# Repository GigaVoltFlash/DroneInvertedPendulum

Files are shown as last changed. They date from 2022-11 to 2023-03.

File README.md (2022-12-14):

# Inverted Pendulum on a CrazyFlie Quadcopter
 
Members: Anshuk Chigullapalli, Rishi Patel, Harry Zhao, Bella Watters

### Abstract
The goal of this project is to create a controller capable of balancing an inverted pendulum on the Crazyflie quadcopter. This is implemented by utilizing the provided sensor decks and the Motion Capture (MoCap) system present in the lab environment. A pendulum is mounted atop the drone with a hinge that allows for one angular degree of freedom. The equations of motion for the pendulum-quadcopter system are derived and linearized about the equilibrium point where the pendulum is in an upright position. The pose of the pendulum is estimated using the MoCap system and tracking markers on both the pendulum and drone. This pose data is then incorporated into the system observer. During testing, the angular error of the pendulum is analyzed to quantify error in the controller and observer performance. Time permitting, the system will be made independent of the MoCap system.

### Equations of Motion
See dynamics/dynamics.ipynb for the full derivation. The equations of motion use the existing drone kinematics and dynamics derived for AE 483, with the additional kinematics of the pendulum based on the state of the drone. The assumption is made that the pendulum's movement does not affect the drone's motion.

### PyBullet Simulation
The Pybullet setup used in AE 483 was modified to have hinge object and the pendulum object so that the controller designed can best tested in simulation before being implemented on the MoCap system.

### Using the MoCap System

1) Setup up the drone pendulum system to have three reflectors, one at the tip of the drone, one at the pendulum base, and a third along the x-axis. 
2) Connect to the "MECHKNIGHT" Wifi network with password "f33dback5". 
3) Open a terminal/command prompt and retrieve your IPv4 address on the network. It should look like 192.168.1.XXX.
4) Navigate to the "DroneInvertedPendulum" directory on the desktop of the MoCap PC. Open the "motrack_udp_InvertedPendulum.py" script in NotePad++.
5) Change the address in the "address_list" array variable to the IPv4 you found earlier.
6) Save and close the file
7) Open the Motive Application located on the desktop of the MoCap PC. When prompted, Click Open Existing Project and choose the AE483 calibration file.
8) You should now see the three reflectors on the drone in the window. Please do not change anything in this file.
9) Navigate back to the "DroneInvertedPendulum" directory on the desktop of the MoCap PC. Double click the "motrack_udp_InvertedPendulum.py". You should see a lot of data scrolling through the terminal.
10) Now, head to your personal laptop and navigate to the "DroneInvertedPendulum" folder and open "motrack_udp_receive_data.py" in the editor of your choice. 
11) Run the file in terminal. Angle data should now be printing in the terminal. Try moving the pendulum to see the change in angle.
12) The angle output should read about 0 degrees. If this is not what you see, please follow the troubleshooting guide below.

### MoCap Troubleshooting

If the angle being printed into the terminal is not correct, there are several reasons this could be happening. The number 1 reason is the order of the motion capture balls in the code is not the same as the order being sent from the central MoCap Computer. In order to fix this, rest the drone-pendulum system in the center of the room with the pendulum on the negative side of the drone. Head over to the MoCap Computer and verify the visual is the same as real life. On the drone operator's laptop, open "motrack_udp_receive_data.py" in the editor of choice and uncomment lines 47 and 49. When the script is run, the terminal will output the positions of each reflective ball every 4 seconds. As seen from lines 24-26, the order of positions printed should be reference, tip, and base. It is possible to guess and check until the angle printed out is correct, however using the Motive software is much easier. First, select the reference ball, right click and hover over "Marker Information". You will see the position of the ball. Compare this to the output on the terminal and check if it is the first position vector printed. If not, look to lines 29-31, and swap variable names until the the vector of reference is printed first. Repeat these steps for each ball until the positions are printed out in the correct order. Once done, comment lines 47 and 49 and rerun the script. The angle should now be fixed.

All the changes made to the "motrack_udp_receive_data.py" file must be copied to the "optitrack" function in "flightThreaded.py".

The other most common failure point is too many markers in the motion capture zone. Unfortunately, there is not much that can be done besides asking for all markers to be covered or moved out of the zone. 

### Hardware Changes

The pendulum was made using a 1.6mm diameter aluminum rod with a reflective ball at the top and bottom. This was then connected to the drone with a 3D-printed custom hinge design which allowed the pendulum to swing with one degree of freedom. 

<!-- ### File Structure

* client: Contains scripts used for operating the drone and performing analysis on data collected during flight.
* OptiTrack: Contains scripts used for sending and receiving data between the OptiTrack Computer and drone operator's laptop.
* firmware: Contains the firmware code used to fly the drone. -->

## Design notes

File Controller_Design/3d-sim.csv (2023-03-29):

time | x | y | z | yaw | pitch | roll | r | s
0.0 | 0.0 | 0.0 | 0.3 | 0.0 | 0.0 | 0.0 | 0.03 | 0.02
0.01 | 2.0084410951447158e-07 | 1.3466445430764533e-07 | 0.29999999960883894 | -1.0731963329099353e-06 | 0.001790702987514691 | -0.001202214452896583 | 0.030045515383370244 | 0.020030342820481353
0.02 | 3.171419454388033e-06 | 2.130358130715952e-06 | 0.29999999271410766 | -1.5525829664653888e-05 | 0.006796622993694129 | -0.004578704387928822 | 0.030180005595058304 | 0.020119987647211145
0.03 | 1.55690883168409e-05 | 1.0481792278861291e-05 | 0.29999993060991975 | -6.947840647937329e-05 | 0.014328354375281332 | -0.009703338768981214 | 0.03039771498495607 | 0.020265040850415268
0.04 | 4.74580177424557e-05 | 3.20409574414711e-05 | 0.29999964653388383 | -0.00019303728092004728 | 0.02377925678021328 | -0.01621086797086229 | 0.03069000137831669 | 0.02045959812225133
0.05 | 0.00011149090535126223 | 7.552093506544515e-05 | 0.2999987661335527 | -0.0004132656055661006 | 0.034620201826255775 | -0.023782176228600467 | 0.03104608368682208 | 0.020696193024748285
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

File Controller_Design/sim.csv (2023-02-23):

time | x | z | theta | alpha
0.0 | 0.0 | 3.0 | 0.0 | 0.1
0.01 | 0.0009938099400883637 | 3.0000006623058217 | 0.0049364958703125 | 0.10036815819452741
0.02 | 0.001980513859265013 | 3.000002534223643 | 0.01785329482834154 | 0.1014399566462271
0.03 | 0.0029740529008861856 | 3.00000524960894 | 0.0354881585726039 | 0.1031296137757584
0.04 | 0.0039936200840638625 | 3.000008112113386 | 0.05549341878181503 | 0.10532032309093181
0.05 | 0.005061033014511207 | 3.0000100233548737 | 0.07620478319736403 | 0.10788088842796799
0.06 | 0.006198876411322737 | 3.000009506627721 | 0.09646679100843064 | 0.11067720759489727
0.07 | 0.007429221180049643 | 3.000004806604344 | 0.11550119797720995 | 0.11357995422153294
0.08 | 0.008772772555884037 | 2.9999940300350976 | 0.13280785946838367 | 0.11646947072109015
0.09 | 0.010248333896235398 | 2.999975295748309 | 0.14809018318115996 | 0.11923864090800416
0.1 | 0.011872499139155121 | 2.999946871467003 | 0.16119914236564242 | 0.12179432469073985
0.11 | 0.01365950790932549 | 2.999907284398129 | 0.17209130755373775 | 0.12405779209333848
0.12 | 0.015621213887682136 | 2.9998554001045084 | 0.18079746948825073 | 0.12596448045122238
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

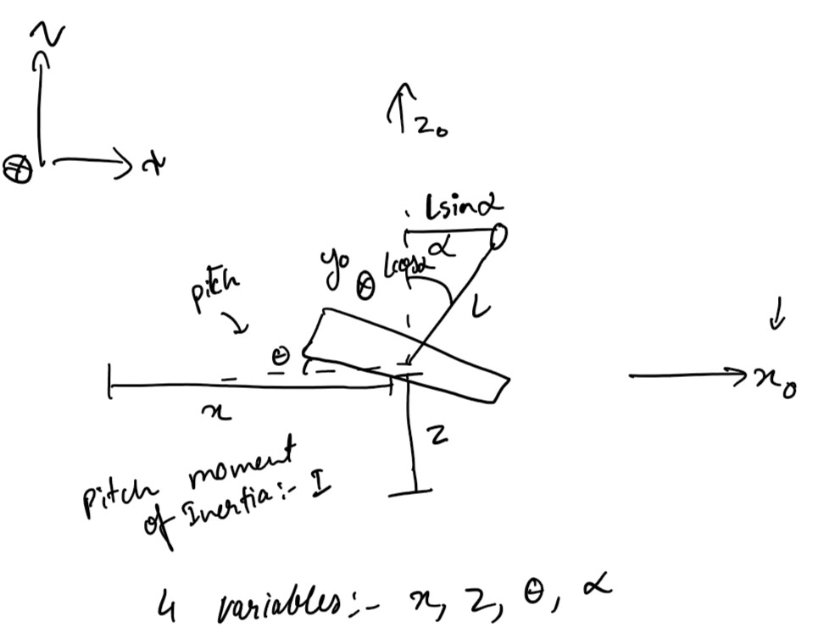
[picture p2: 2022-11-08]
Controller_Design/Inverted_Pendulum_Kinematics.jpg

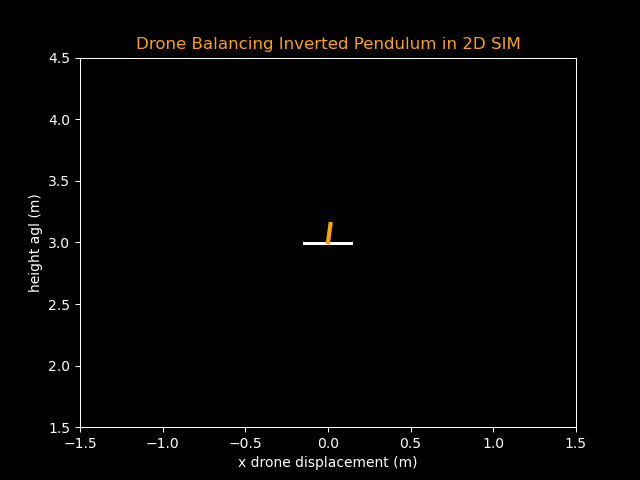
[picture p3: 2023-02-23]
2d_animation.gif

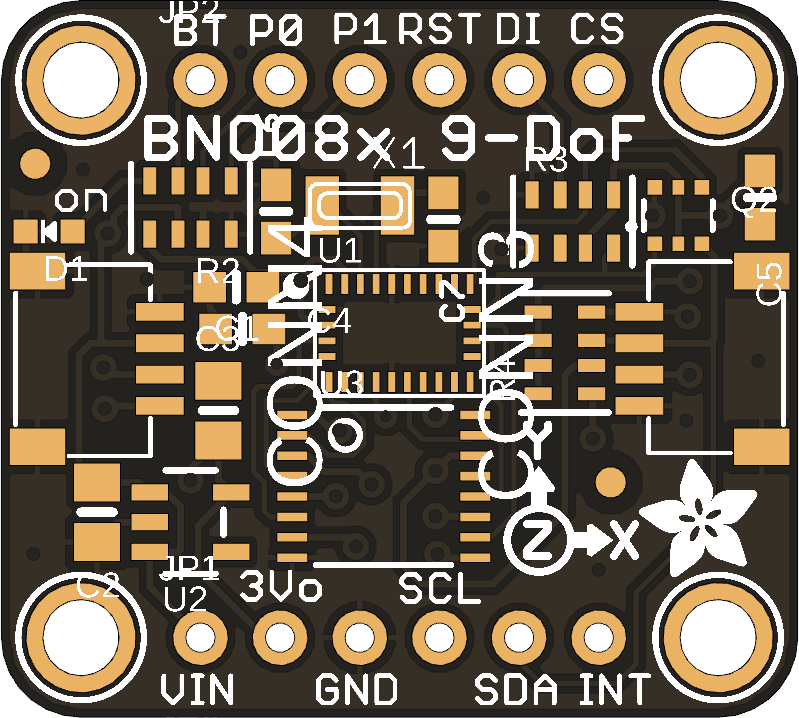
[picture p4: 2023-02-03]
CAD/adafruit-bno085-9-dof-imu-stemma-qt-1.snapshot.3/Adafruit BNO085 STEMMA QT Top.png

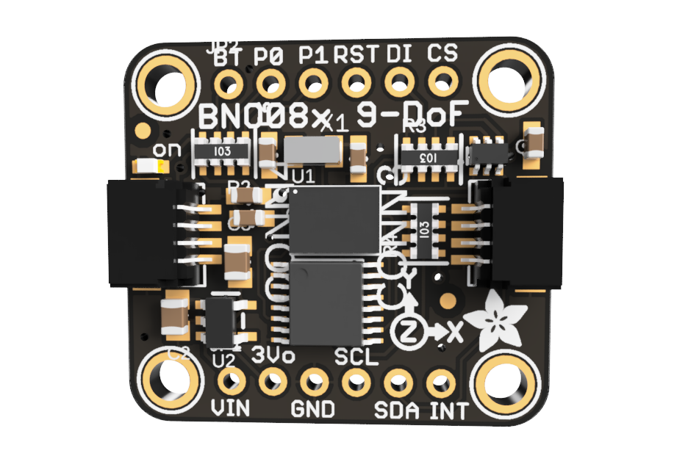
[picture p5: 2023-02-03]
CAD/adafruit-bno085-9-dof-imu-stemma-qt-1.snapshot.3/Adafruit_BNO085_STEMMA_QT.png

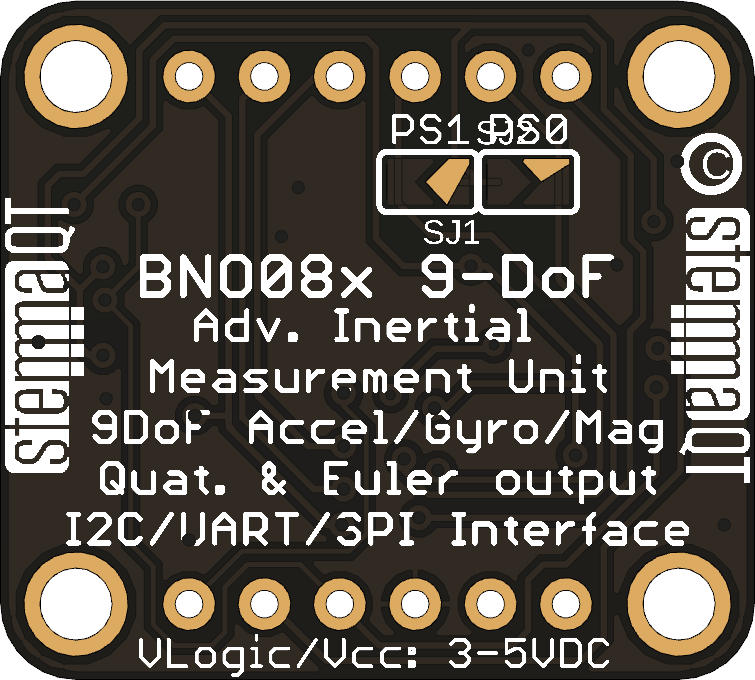
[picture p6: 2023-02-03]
CAD/adafruit-bno085-9-dof-imu-stemma-qt-1.snapshot.3/Adafruit BNO085 STEMMA QT Bottom.png

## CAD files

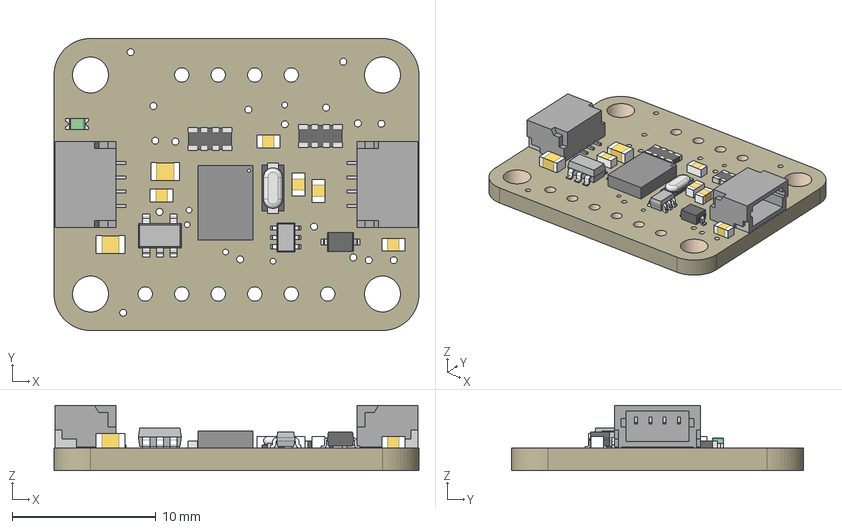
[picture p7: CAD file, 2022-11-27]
CAD/4646 BNO055 Stemma.step
25.4 x 20.3 x 4.53 mm
Board
BNO055
10K x 5
1n4148
10uF x 2
AP2112K-3.3
10K_1 x 2
BSS138
STEMMA_I2C_QT x 2
GREEN

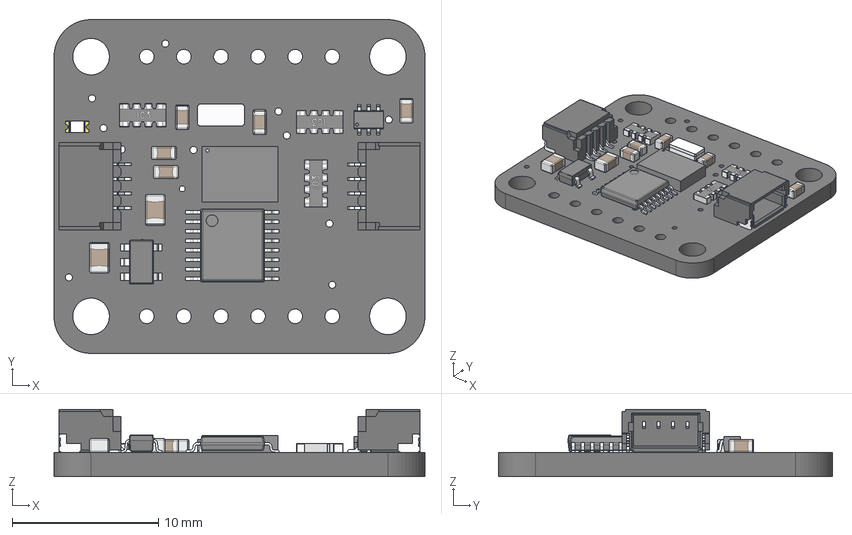
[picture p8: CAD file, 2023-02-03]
CAD/adafruit-bno085-9-dof-imu-stemma-qt-1.snapshot.3/Adafruit BNO085 STEMMA QT.step
25.4 x 22.9 x 4.60 mm
Printed Circuit Board
BNO055-9axis-IMU
BNO085-9axis-IMU
BODY-TSSOP
LEAD-TSSOP x 16
Crystal_XTAL3215_32.768KHz
SOT23-5
BSS138PS
LED 0603 single color
CAPC-0805-T0.95-BN x 2
CAPC-0603-T0.9-BN x 5
YC164_RESPACK x 3
qwicc x 2

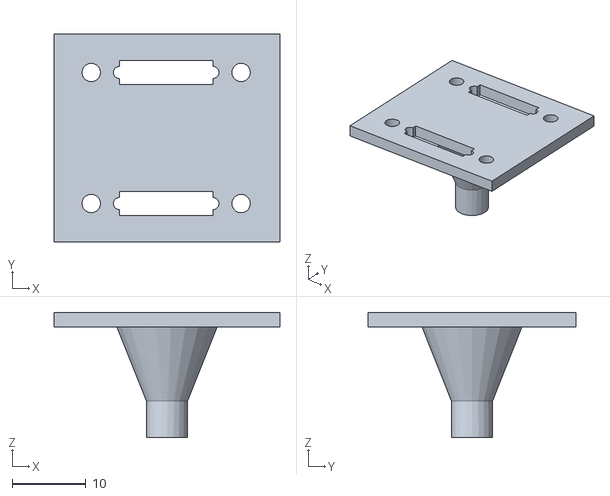
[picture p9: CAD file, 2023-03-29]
CAD/STL Files/BNO_mount_flat.stl
30.6 x 28.2 x 17.0

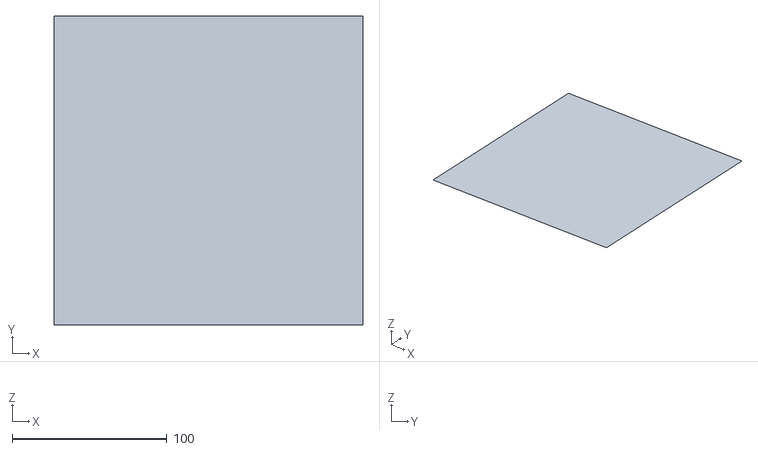
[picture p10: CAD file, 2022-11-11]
Controller_Design/urdf/plane.obj
200.0 x 200.0 x 0

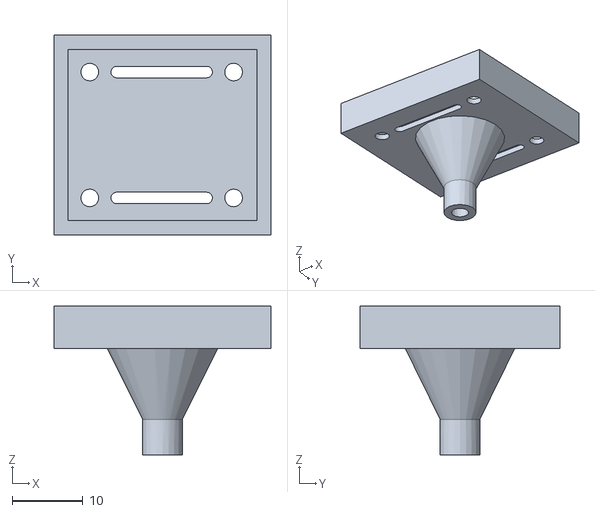
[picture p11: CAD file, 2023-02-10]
CAD/STL Files/BNO_mount_adjusted.stl
30.6 x 28.2 x 21.0

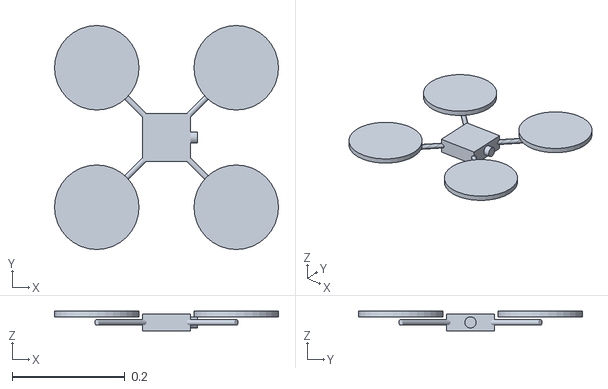
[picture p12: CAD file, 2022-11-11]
Controller_Design/urdf/drone.stl
0.397 x 0.397 x 0.035

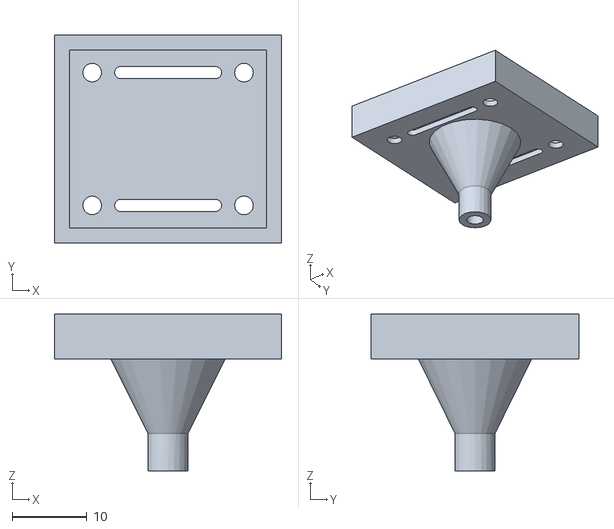
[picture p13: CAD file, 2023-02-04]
CAD/STL Files/BNO_mount.stl
30.4 x 27.9 x 21.0

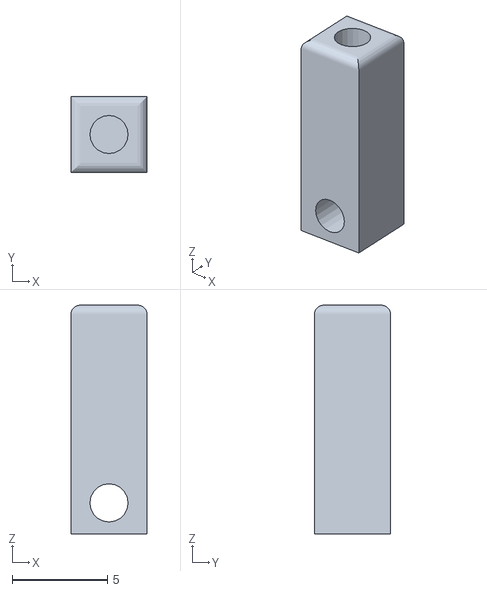
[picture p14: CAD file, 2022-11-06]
CAD/STL Files/SwivelBlock.stl
4.00 x 4.00 x 12.0

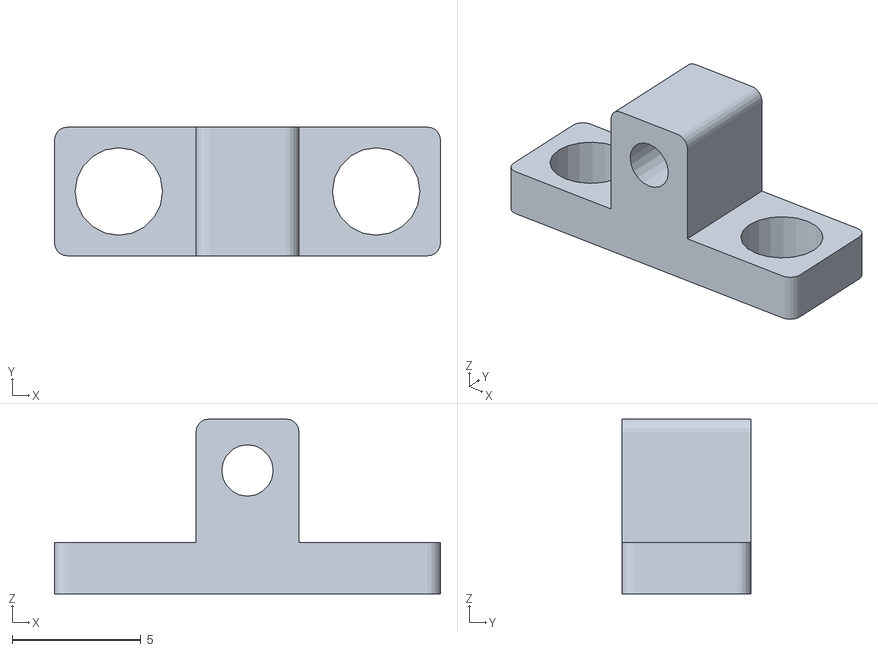
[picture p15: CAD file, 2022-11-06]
CAD/STL Files/SwivelBase.stl
15.0 x 5.00 x 6.80

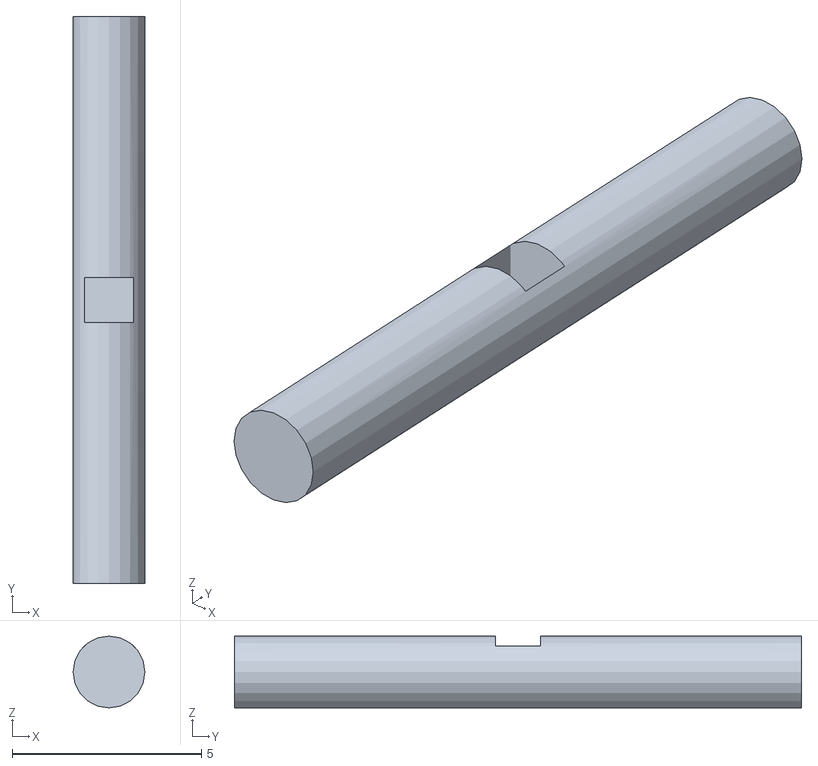
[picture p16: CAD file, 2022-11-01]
CAD/STL Files/SwivelPeg.stl
1.90 x 15.0 x 1.90

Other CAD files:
CAD/10K.prt
CAD/10K_1.prt
CAD/10uF.prt
CAD/1n4148.prt
CAD/32.768.prt
CAD/4646 BNO055 Stemma_step.prt
CAD/AP2112K-3.3.prt
CAD/BNO055.prt
CAD/BNO_mount.prt
CAD/BNO_mount_assembly.prt
CAD/BSS138.prt
CAD/Board.prt
CAD/GREEN.prt
CAD/PRT Files/CrazyflieLayout.prt
CAD/PRT Files/MoCapDeck.prt
CAD/PRT Files/PendulumAssembly.prt
CAD/PRT Files/PendulumRod.prt
CAD/PRT Files/SwivelBase.prt
CAD/PRT Files/SwivelBlock.prt
CAD/PRT Files/SwivelPeg.prt
CAD/STEMMA_I2C_QT.prt
CAD/adafruit-bno085-9-dof-imu-stemma-qt-1.snapshot.3/Adafruit BNO085 STEMMA QT.f3d
CAD/adafruit-bno085-9-dof-imu-stemma-qt-1.snapshot.3/Adafruit BNO085 STEMMA QT_step.prt
CAD/adafruit-bno085-9-dof-imu-stemma-qt-1.snapshot.3/BNO055-9axis-IMU.prt
CAD/adafruit-bno085-9-dof-imu-stemma-qt-1.snapshot.3/BNO085-9axis-IMU.prt
CAD/adafruit-bno085-9-dof-imu-stemma-qt-1.snapshot.3/BODY-TSSOP.prt
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

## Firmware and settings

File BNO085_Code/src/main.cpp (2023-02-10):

#include <Arduino.h>
#include <Adafruit_BNO08x.h>
#include "IMU.h"
#include <math.h>

#define BNO08X_RESET -1

// Adafruit_BNO08x bno08x(BNO08X_RESET);

Adafruit_BNO08x bno(BNO08X_RESET);
IMU imu;
euler_t euler;
void setup() {
  // put your setup code here, to run once:
  Serial.begin(115200);
  while (!Serial) delay(10);
  // Try to initialize!
  if (!bno.begin_I2C()) {
      // if (!bno08x.begin_UART(&Serial1)) {  // Requires a device with > 300
      // byte UART buffer! if (!bno08x.begin_SPI(BNO08X_CS, BNO08X_INT)) {
      Serial.println("Failed to find BNO08x chip");
      while (1) {
          delay(10);
      }
  }
  imu = IMU(&bno);
  // imu.setIMU(&bno);


}

void loop() {
  // put your main code here, to run repeatedly:
  imu.readData();
  euler = imu.getEuler();
  // float l = 62.0; // cm
  // float r_disp = l*(sin(euler.pitch));
  // float s_disp = -l*(sin(euler.roll)*cos(euler.pitch));
  Serial.print("Yaw: ");
  Serial.print(euler.yaw);
  Serial.print("  |||  Pitch: ");
  Serial.print(euler.pitch);
  Serial.print("  |||  Roll: ");
  Serial.println(euler.roll);
  // Serial.print("  |||  Displacement in World X: ");
  // Serial.print(r_disp);
  // Serial.print("  |||  Displacement in World Y: ");
  // Serial.println(s_disp);
  delay(100);
}

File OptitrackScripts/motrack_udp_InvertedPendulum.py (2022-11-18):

    ###########################################################################
#   motrack_udp_multi.py
#
#   v1.0.0
#   written by Miles Johnson, Aaron Phelps, and Cem Onglsku
#
#   reads 6-DOF on multiple trackables from a running Tracking Tools
#   (go to Streaming Pane and check the box for 'Broadcast Frame Data'
#   in NaturalPoint Streaming Engine, For "Network Interface Selection",
#   under "Local Interface" set to <opti_ip> ) and sends the data to
#   <drone_ip>, a list of IPs for laptops running drones.
#
#    Note that the order of IP addresses in drone_ip corresponds to the
#    trackable numbers.  These must match!
#
#    Copies of this code are found on the svn at
# https://subversion.cs.illinois.edu/svn/ae483/trunk/optitrack/motrack_udp_multi.py
# -------------------------------------------------------------------------
#   Change Log:
#
#   
###########################################################################

import sys
import socket
import struct
import threading
import time
import math

import serial
import Queue
import fmcore
import scipy.io
from policies import lqr_outer

from utils import *


##################################################################
######## Configuration Options ###################################
##################################################################

# Drone Computer IP's - First IP responds to first trackable, etc.
# To increase number of drones, add IP's (run "ifconfig eth0" on Linux machines)
#drone_ip = ["192.168.0.109"]
#drone_ip = "192.168.1.51", "192.168.1.52","192.168.1.54"
# drone_ip = "192.168.0.51", "192.168.0.52","192.168.0.54"
#drone_ip = ["192.168.1.72"]

# Drone Computer UDP Port
#drone_port = 3500
udp_port = 3500
# address_list = ["192.168.1.166"]
address_list = ["192.168.1.103"]

            
# OptiTrack Computer IP address
# [Start->type 'cmd' in command window, type IPconfig, IPv4]
# opti_ip ="192.168.1.99"
opti_ip ="192.168.0.99"

# Data Port Set in Optitrack Streaming Properties
opti_port = 1511

# Multicast Interface in Optitrack Streaming Properties
multicastAdd = "239.255.42.99"

##################################################################
##################################################################
# DO NOT EDIT ANYTHING BENEATH THIS LINE!!!!
##################################################################
##################################################################

def unPack(data):
    trackableState = []
    markerState = []
    byteorder='@'
    PacketIn = data
    major = 2
    minor = 0
    offset = 0
    # message ID, nBytes
    messageID, nBytes = struct.unpack(byteorder+'hh',PacketIn[offset:offset+4])
    offset += 4
    #print 'messageID=',messageID,' number of bytes=',nBytes
    if (messageID == 7):
        frameNumber,nMarkerSets = struct.unpack(byteorder+'ii',PacketIn[offset:offset+8])
        offset += 8
        #print 'Markersets=', nMarkerSets
        i=nMarkerSets
        while (i > 0):
            ns = PacketIn[offset:offset+255]
            szNamelen=ns.find('\0')
            #print ns, szNamelen
            szName = struct.unpack(byteorder+str(szNamelen)+'s',PacketIn[offset:offset+szNamelen])[0]
            offset += szNamelen+1 # include the C zero char
            #print 'Modelname=',szName
            # markers
            nMarkers = struct.unpack(byteorder+'i',PacketIn[offset:offset+4])[0]
            offset += 4
            #print 'Markercount=',nMarkers
            j=nMarkers
            while (j>0):
                x,y,z = struct.unpack(byteorder+'fff',PacketIn[offset:offset+12])
                offset += 12
                j=j-1
            i=i-1

        #unidentified markers
        nUMarkers = struct.unpack(byteorder+'i',PacketIn[offset:offset+4])[0]
        offset += 4
        #print 'Unidentified Markercount=',nUMarkers
        i = nUMarkers
        while (i > 0):
            ux,uy,uz = struct.unpack(byteorder+'fff',PacketIn[offset:offset+12])
            offset += 12
            markerState.append([ux,uy,uz])
            #print [ux,uy,uz]
            i=i-1

        # rigid bodies
        nrigidBodies = struct.unpack(byteorder+'i',PacketIn[offset:offset+4])[0]
        nr = nrigidBodies
        #print nr
        offset += 4
        #print 'Rigid bodies=',nrigidBodies
        while (nr > 0):
            ID = struct.unpack(byteorder+'i',PacketIn[offset:offset+4])[0]
            offset += 4
            rbx,rby,rbz = struct.unpack(byteorder+'fff',PacketIn[offset:offset+12])
            offset += 12
            rbqx,rbqy,rbqz,rbqw = struct.unpack(byteorder+'ffff',PacketIn[offset:offset+16])
            offset += 16

            trackableState.append([ID,frameNumber, rbx, rby, rbz, rbqw, rbqx, rbqy, rbqz])  # our quaternion convention is scalar part first!

            #print '\nID=',ID
            #print 'pos:',rbx,rby,rbz
            #print 'ori:',rbqx,rbqy,rbqz,rbqw
            # associated marker positions
            nRigidMarkers = struct.unpack(byteorder+'i',PacketIn[offset:offset+4])[0]
            offset += 4
            #print 'Marker count=',nRigidMarkers
            md = []
            markerID = []
            markersize = []
            for i in range(0,nRigidMarkers):
                md.extend(struct.unpack(byteorder+'fff',PacketIn[offset:offset+12]))
                offset += 12
            if major >= 2:
                for i in range(0,nRigidMarkers):
                    markerID.append(struct.unpack(byteorder+'I',PacketIn[offset:offset+4])[0])
                    offset += 4
                for i in range(0,nRigidMarkers):
                    markersize.append(struct.unpack(byteorder+'f',PacketIn[offset:offset+4])[0])
                    offset += 4
                for i in range(0,nRigidMarkers):
                    pass
                    #print 'Marker ',i+1,' ID=',markerID[i],' markerData=',md[3*i],md[3*i+1],md[3*i+2],' markersize=',markersize[i]
            else:
                for i in range(0,nRigidMarkers):
                    pass
                    #print 'Marker ',i+1,' markerData=',md[3*i],md[3*i+1],md[3*i+2]

            # marker errors
            if major >= 2:
                markerError = struct.unpack(byteorder+'f',PacketIn[offset:offset+4])[0]
                offset += 4
                #print 'Mean marker error=',markerError

            nr = nr-1 # next rigid body
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

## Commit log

2022-11-01 Created Hinge System for Pendulum
    [CrazyflieLayout.prt, MoCapDeck.prt, PendulumAssembly.prt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]
2022-11-01 STL Files
    [SwivelBase.stl, SwivelPeg.stl]
2022-11-09 Created PyBullet simulation
    [drone.stl, drone.urdf, frame.urdf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]
2022-11-16 Slight changes to urdf and controller gains
    [drone.urdf]
2022-11-18 Cleaned up repo
    [CrazyflieLayout.prt, MoCapDeck.prt, PendulumAssembly.prt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]
2022-12-14 Combined notebooks and updated directories
    [drone.stl, drone.urdf, frame.urdf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]
2023-01-20 Figuring out annoying issues with simulation
    [drone.urdf]
2023-01-22 added drone animation in 2D
    [sim.csv]
2023-01-22 minor animation fixes
    [sim.csv]
2023-01-23 Misc. changes and playing with 2D sim
    [sim.csv]
2023-02-03 Added the bno holder
    [Adafruit BNO085 STEMMA QT.f3d, Adafruit BNO085 STEMMA QT.step, Adafruit BNO085 STEMMA QT_step.prt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]
2023-02-04 Sim of pendulum and controller working
    [BNO_mount.stl, BNO_mount_assembly.prt]
2023-02-09 testing realistic conditions of pendulum initial conditions
    [sim.csv]
2023-02-10 Adjusted tolerances mount
    [BNO_mount.prt, BNO_mount_adjusted.stl, BNO_mount_assembly.prt]
2023-02-15 added basic 3-D Drone Animation without pendulum
    [3d-sim.csv, sim.csv]
2023-02-23 Random runs
    [sim.csv]
2023-03-18 Fixed some issues in the 3D sim
    [3d-sim.csv]
2023-03-21 We now have two versions of the sim, and the controller tuning is underway
    [3d-sim.csv]
2023-03-26 Controller tuning
    [3d-sim.csv]
2023-03-27 new moments/masses
    [3d-sim.csv]
2023-03-29 controller stuff
    [3d-sim.csv]
2023-03-29 new BNO code
    [BNO_mount.prt, BNO_mount_flat.stl]
